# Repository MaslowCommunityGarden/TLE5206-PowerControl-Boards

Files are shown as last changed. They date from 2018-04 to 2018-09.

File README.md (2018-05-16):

# TLE5206 PowerControl Boards

PowerControl board based on the TLE5206. Thru-hole and SMD versions

# About the boards:

The standard Maslow PowerControl board uses a pair of simple surface-mount motor-control chips, the L298P013TR, to control the motors. Each chip can control two motors, up to total 4A divided between the motors. Only three motors are provisioned in the release version of the board. There has been concern about the current capacity of these chips and there have been instances where the chips have been damaged when software malfunctioned. Once a chip is damaged, the board would require replacing a 20-pin surface-mount chip to repair.

The TLE5206 offers higher current capacity, over-temperature and over-current detection and protection, along with a simpler package. In addition, there is a thru-hole version of the chip available that would allow a thru-hole version of the board, easier for some users to construct or repair. While the control pins are different from the L298 chips, the firmware requires very little change to work with the TLE5206.

This is a first stab at using the TLE5206 chips on the PowerControl board.
 -  The Electronics folder has EagleCAD board and schematic files for a SMD version and a thru-hole version. I've built and tested both.
 -  The Firmware has been merged with the main MaslowCNC Firmware branch. It adds three true PWM pins to the AUX group which might be used for spindle control with some software development. It doesn't implement the software over-current detection that the TLE5206 offers. For now, the chips sense the over-current or over-temperature condition and protect themselves by turning off the outputs. Use the Arduino IDE to upload the master firmware to control the TLE5206 board.

This design brings:
- separate controller chip for each motor
- higher current capacity (5A) per motor
- thru-hole version to aid hand assembly and repair
- board-mounted heat sinks for the thru-hole version
- mounting holes to match three of the Arduino mounting holes
- AUX pins moved to extended end of board
- 4 digital AUX pins
- 2 analog/digital AUX pins
- 3 PWM-capable digital AUX pins
- board version ID pins avoids using SPI pins

It doesn't bring:
- additional motor control channels
- software over-current or over-temperature sensing

# PCBs
======================

Layout

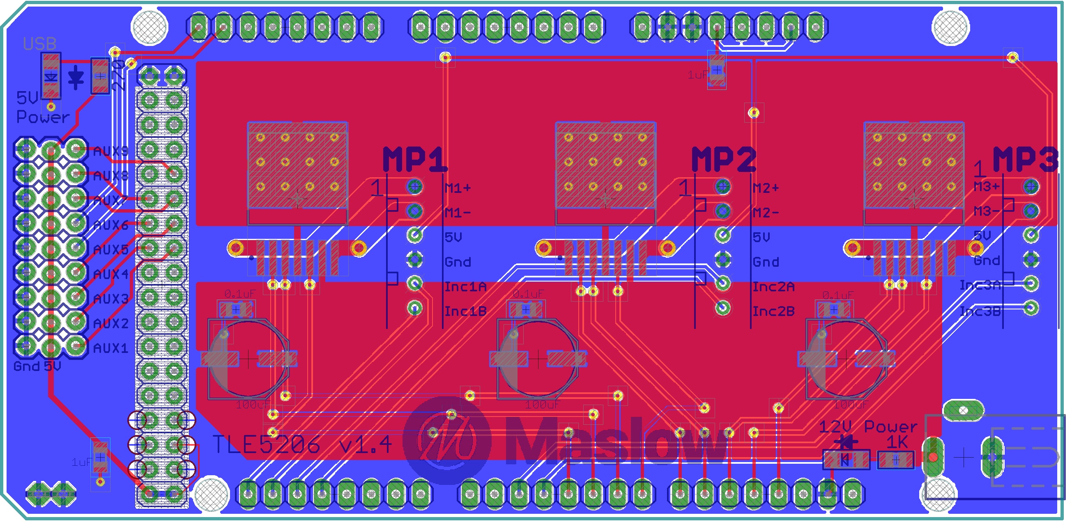
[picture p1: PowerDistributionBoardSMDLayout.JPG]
SMD Layout


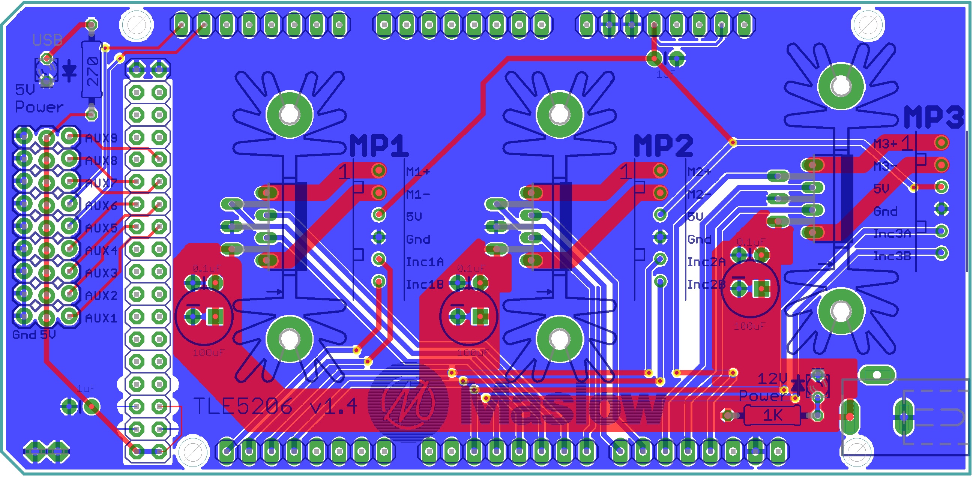
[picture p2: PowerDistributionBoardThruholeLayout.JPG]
Thruhole Layout


Schematic - SMD version

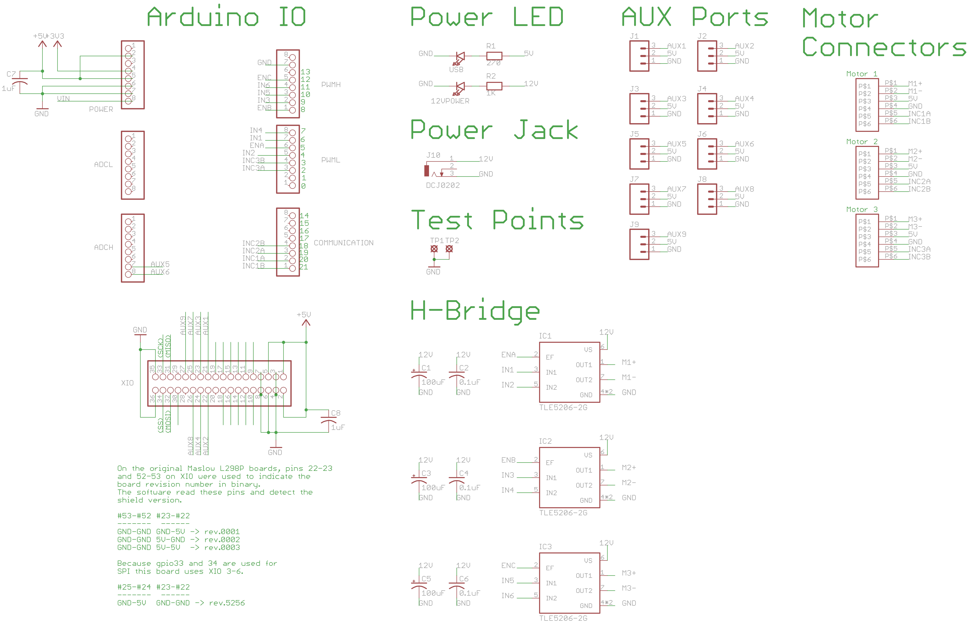
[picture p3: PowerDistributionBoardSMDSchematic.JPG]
SMD schematic


Schematic - Thruhole version

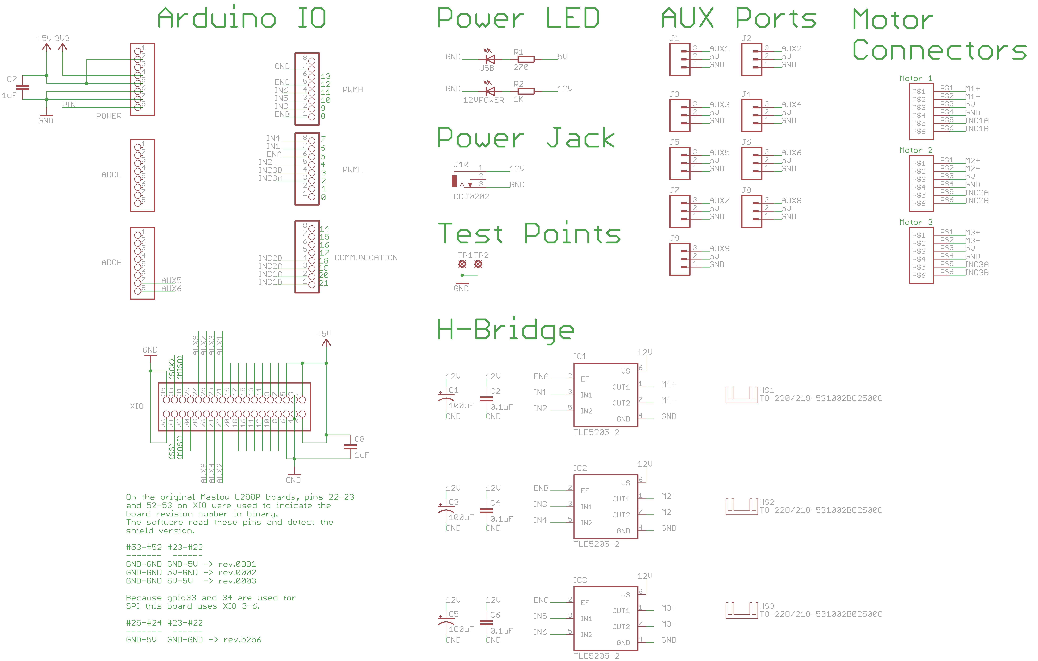
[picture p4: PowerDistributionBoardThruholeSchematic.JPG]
Thruhole Schematic


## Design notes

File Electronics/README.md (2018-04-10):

Maslow PCBs
======================

The TLE5206 offers over-temperature and over-current detection and protection.

This design brings:
- separate controller chip for each motor
- higher current capacity (5A) per motor
- thru-hole parts to aid hand assembly and repair
- board-mounted heat sinks for the thru-hole version
- mounting holes to match the Arduino Mega2560
- AUX pins on extended end of board
- 4 digital AUX pins
- 2 analog/digital AUX pins
- 3 PWM-capable AUX pins
- board version ID pins avoids using SPI pins

Layout
  - thru-hole
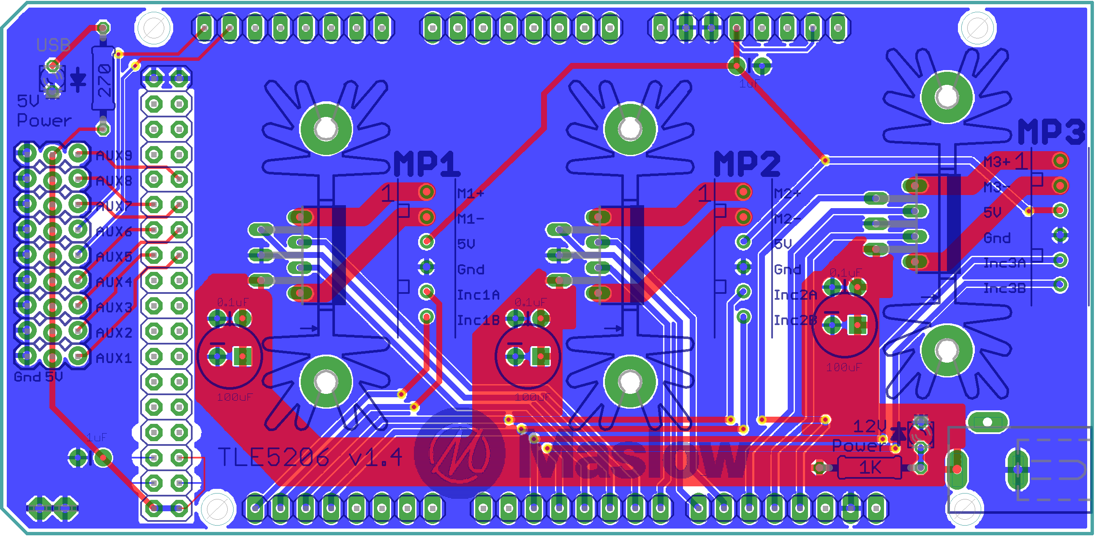
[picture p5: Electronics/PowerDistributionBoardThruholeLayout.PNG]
Layout

  - SMD
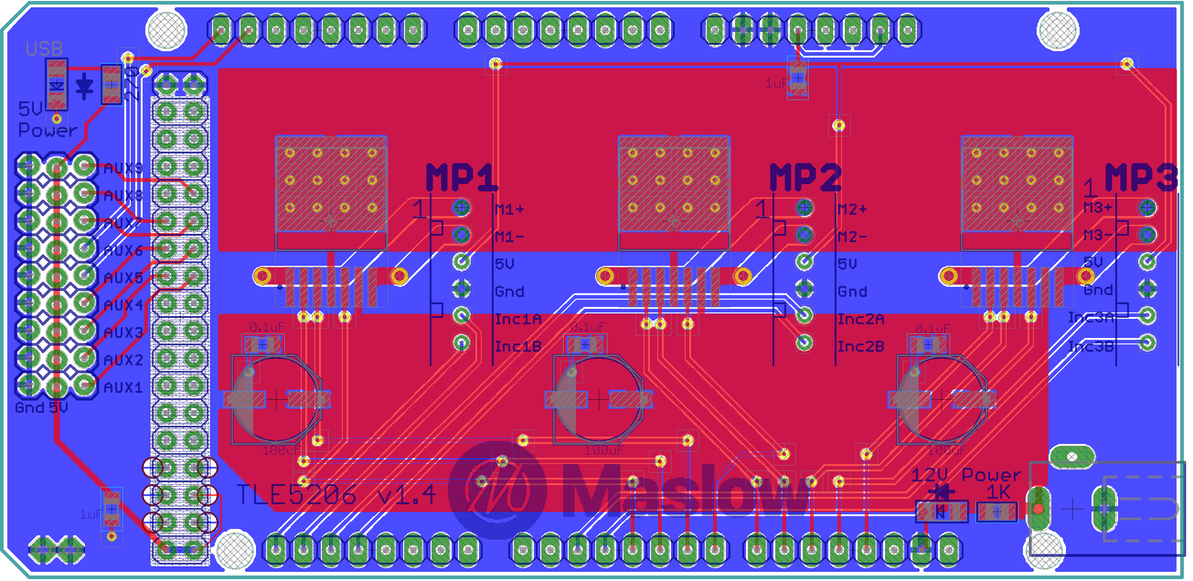
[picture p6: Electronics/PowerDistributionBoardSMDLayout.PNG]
Layout


Schematic
- thru-hole
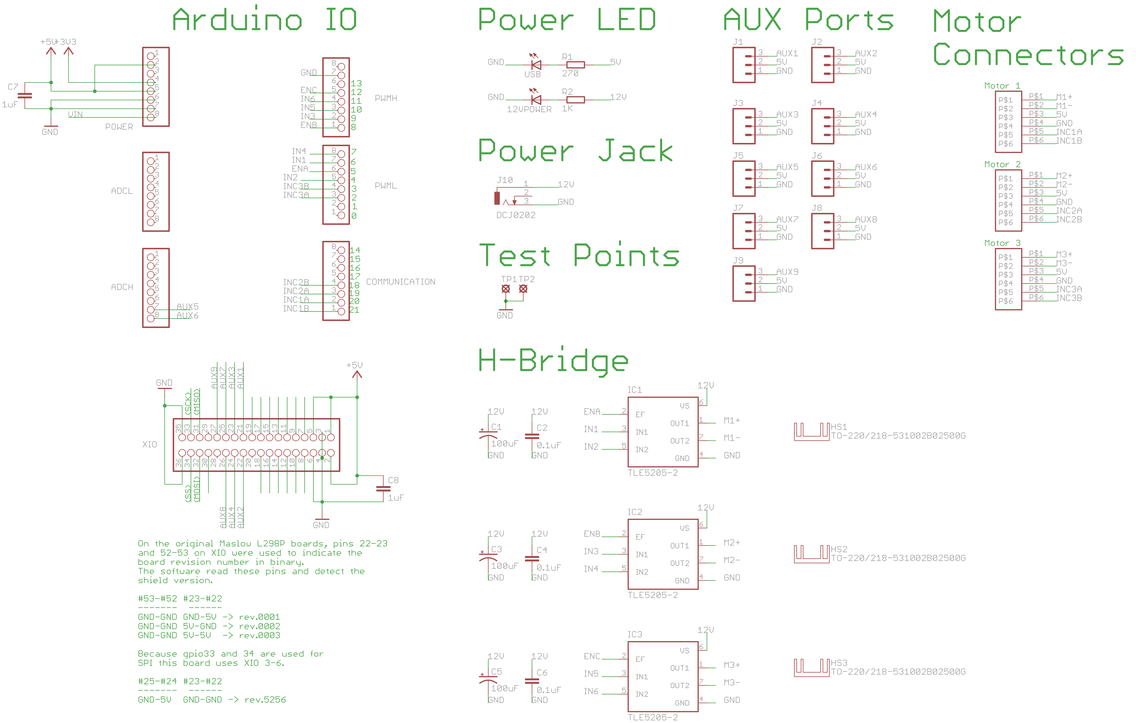
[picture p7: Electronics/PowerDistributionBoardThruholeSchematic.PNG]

- SMD
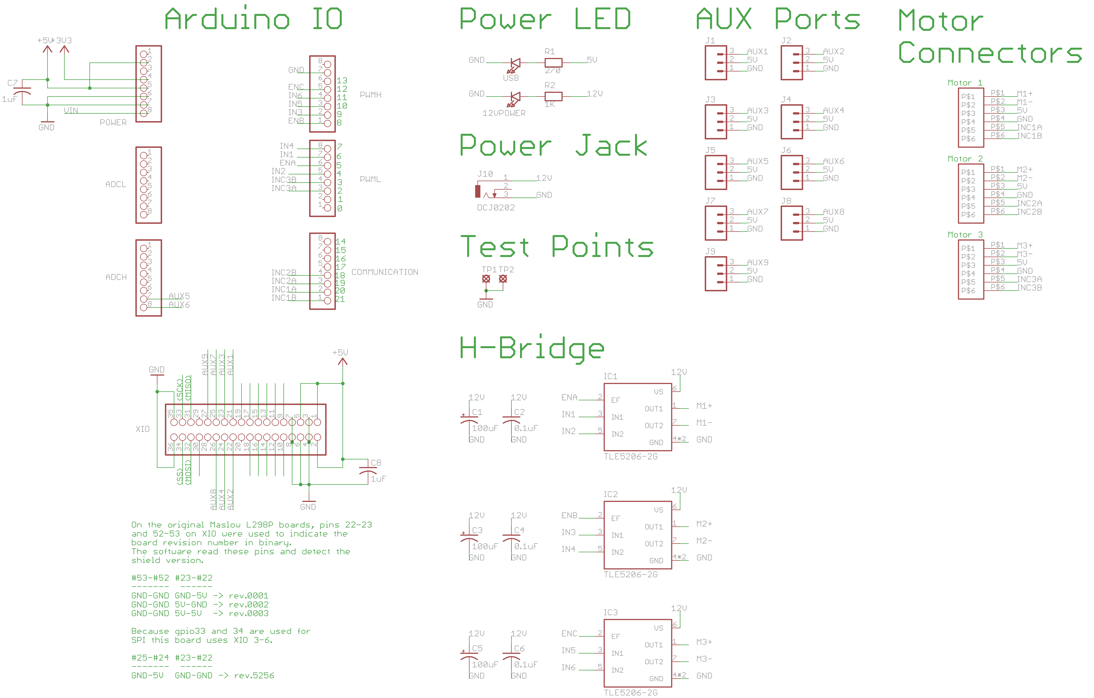
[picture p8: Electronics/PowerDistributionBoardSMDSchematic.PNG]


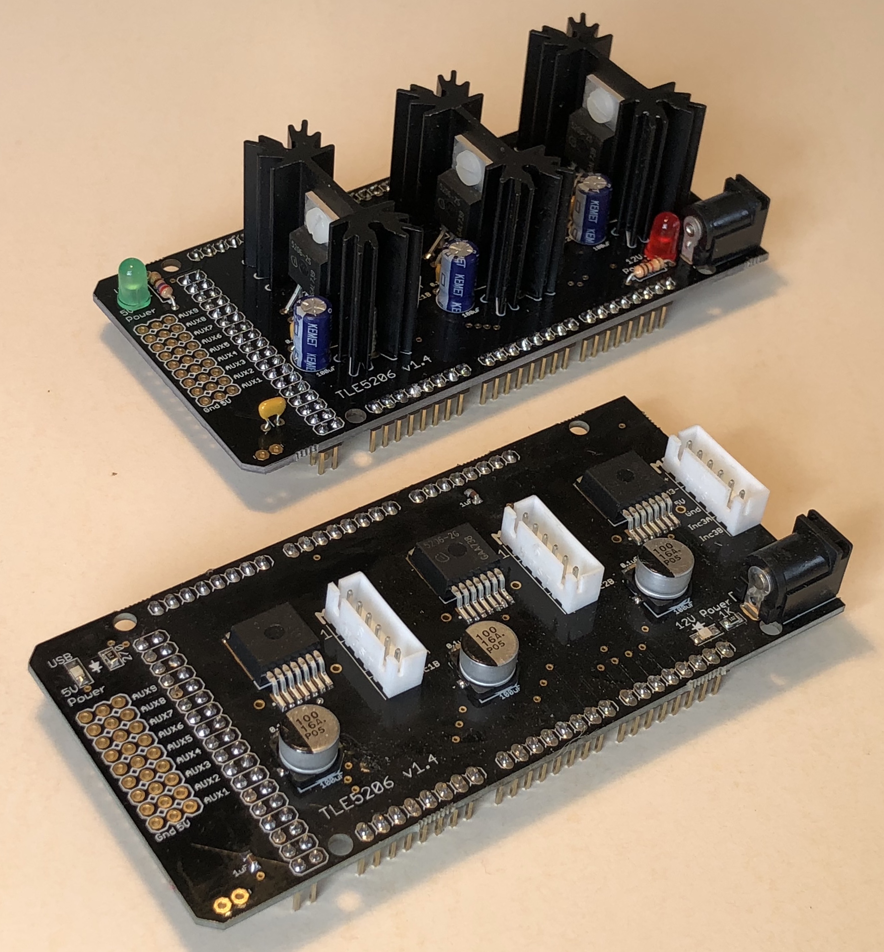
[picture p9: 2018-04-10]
mainpicture.jpg

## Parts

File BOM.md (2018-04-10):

The Electronics folder has BOM files for both versions of the board. Many web-based PCB houses accept an EagleCAD .brd file for ordering.
The Firmware has the branch of Firmware to use the boards.

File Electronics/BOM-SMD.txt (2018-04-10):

PCB BOM SMD

XH-Series Connectors: 455-2271-ND             3        MP1-3
Power Jack:           CP-202BH-ND             1        J10
1x8 .1" headers:      732-5321-ND             6        Arduino Pwr, ADCL, ADCH, Comm., PWML, PWMH
18x2 .1" headers:     732-5309-ND             1        XIO
H-Bridge:             TLE52062GAUMA1CT-ND     3        IC-1,2,3
Indicator LED Green:  475-1410-1-ND           2        LED 1: 5V, LED 2: 12V
Current Limiting R1:  RMCF0805JT270RCT-ND     1        R1
Current Limiting R2:  541-4162-1-ND           1        R2
25.4x34.93mm heatsink Mouser-532-374124B35G   3        N/A
Capacitors 100uF      PCE3879DKR-ND           3        C1, C3, C5
Capacitors 1uF        445-5146-1-N            2        C7,8
Capacitors 0.1uF      311-1361-1-ND           3        C2, C4, C6

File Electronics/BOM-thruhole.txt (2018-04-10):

PCB BOM-trhuhole

XH-Series Connectors: 455-2271-ND             3        MP1-3
Power Jack:           CP-202BH-ND             1        J10
1x8 .1" headers:      732-5321-ND             6        Arduino Pwr, ADCL, ADCH, Comm., PWML, PWMH
18x2 .1" headers:     732-5309-ND             1        XIO
H-Bridge:             TLE52062SAKSA1-ND       3        IC-1,2,3
Indicator LED Green:  160-1130-ND             1        LED 1: 5V
Indicator LED Red:    160-1127-ND             1        LED 2: 12V
Current Limiting R1:  1263-CF14JB270R-CHP     1        R1
Current Limiting R2:  1.0KQBK-ND              1        R2
25.4x34.93mm heatsink HS351-ND                3        N/A
Capacitors 100uF      399-6650-1-ND           3        C1, C3, C5
Capacitors 1uF        BC1168CT-ND             2        C7,8
Capacitors 0.1uF      BC1101CT-ND             3        C2, C4, C6
#4-40 x 1/4" Panhead Nylon machine screws     3
#4-40 nylon nuts                              3

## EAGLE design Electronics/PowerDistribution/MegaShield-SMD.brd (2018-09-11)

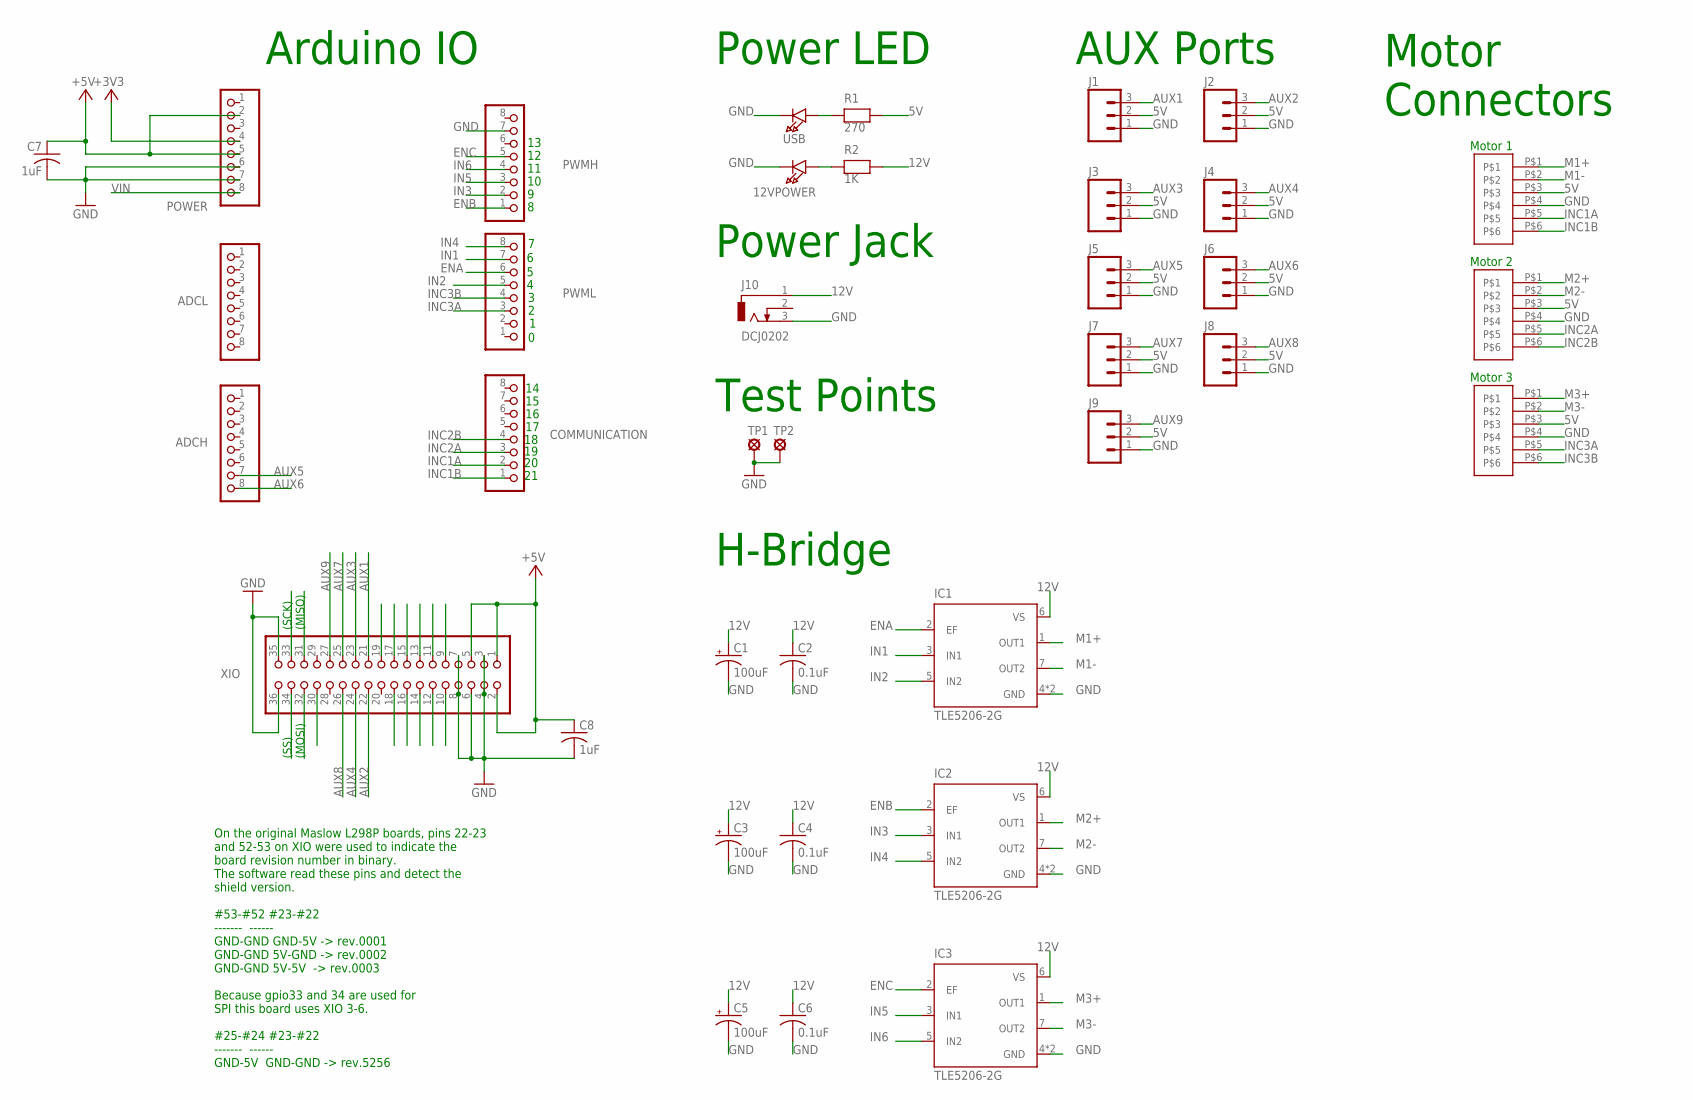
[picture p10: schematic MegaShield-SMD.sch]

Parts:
12VPOWER: LED1206; CHIPLED_1206
ADCH: 8x1F-H8.5; 1X08
ADCL: PINHD-1X8; 1X08
C1, C3, C5: 100uF; PANASONIC_E
C2, C4, C6: 0.1uF; C0805K
C7, C8: 1uF; C0805K
COMMUNICATION: PINHD-1X8; 1X08
IC1, IC2: TLE5206-2G; INF-PG-TO263-7-1_L_1PRIMARY
IC3: TLE5206-2G; INF-PG-TO263-7-1_L_1PRIMARY; DIGIKEY TLE5206-2S-ND
J1, J2, J3, J4, J5, J6, J7, J8, J9: M03LOCK; 1X03_LOCK
J10: DCJ0202
MP1, MP2, MP3: JST-PH-6; JST-PHR-6-SMD
POWER: 8x1F-H8.5; 1X08
PWMH: PINHD-1X8; 1X08
PWML: PINHD-1X8; 1X08
R1: 270; 0805
R2: 1K; 0805
TP1, TP2: LSP10
USB: LED1206; CHIPLED_1206
XIO: 18x2F-H8.5; 2X18

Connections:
5V: C7.1, C8.1, J1.2, J2.2, J3.2, J4.2, J5.2, J6.2, J7.2, J8.2, J9.2, MP1.P$3, MP2.P$3, MP3.P$3, POWER.2, POWER.5, R1.2, XIO.1, XIO.2, XIO.5
12V: C1.+, C2.1, C3.+, C4.1, C5.+, C6.1, IC1.6 (VS), IC2.6 (VS), IC3.6 (VS), J10.1, R2.2
+3V3: POWER.4
AUX1: J1.3, XIO.21
AUX2: J2.3, XIO.22
AUX3: J3.3, XIO.23
AUX4: J4.3, XIO.24
AUX5: ADCH.7, J5.3
AUX6: ADCH.8, J6.3
AUX7: J7.3, XIO.25
AUX8: J8.3, XIO.26
AUX9: J9.3, XIO.27
ENA: IC1.2 (EF), PWML.6
ENB: IC2.2 (EF), PWMH.1
ENC: IC3.2 (EF), PWMH.5
GND: 12VPOWER.C, C1.-, C2.2, C3.-, C4.2, C5.-, C6.2, C7.2, C8.2, IC1.4 (GND), IC1.8 (GND), IC2.4 (GND), IC2.8 (GND), IC3.4 (GND), IC3.8 (GND), J1.1, J2.1, J3.1, J4.1, J5.1, J6.1, J7.1, J8.1, J9.1, J10.3, MP1.P$4, MP2.P$4, MP3.P$4, POWER.6, POWER.7, PWMH.7, TP1.MP, TP2.MP, USB.C, XIO.3, XIO.4, XIO.6, XIO.7, XIO.8, XIO.35, XIO.36
IN1: IC1.3 (IN1), PWML.7
IN2: IC1.5 (IN2), PWML.5
IN3: IC2.3 (IN1), PWMH.2
IN4: IC2.5 (IN2), PWML.8
IN5: IC3.3 (IN1), PWMH.3
IN6: IC3.5 (IN2), PWMH.4
INC1A: COMMUNICATION.2, MP1.P$5
INC1B: COMMUNICATION.1, MP1.P$6
INC2A: COMMUNICATION.3, MP2.P$5
INC2B: COMMUNICATION.4, MP2.P$6
INC3A: MP3.P$5, PWML.3
INC3B: MP3.P$6, PWML.4
M1+: IC1.1 (OUT1), MP1.P$1
M1-: IC1.7 (OUT2), MP1.P$2
M2+: IC2.1 (OUT1), MP2.P$1
M2-: IC2.7 (OUT2), MP2.P$2
M3+: IC3.1 (OUT1), MP3.P$1
M3-: IC3.7 (OUT2), MP3.P$2
unnamed: R1.1, USB.A
unnamed: 12VPOWER.A, R2.1
PA6: XIO.9
PA7: XIO.10
PB0: XIO.34
PB1: XIO.33
PB2: XIO.32
PB3: XIO.31
PC0: XIO.18
PC1: XIO.17
PC2: XIO.16
PC3: XIO.15
PC4: XIO.14
PC5: XIO.13
PC6: XIO.12
PC7: XIO.11
PD7: XIO.19
PL0: XIO.30
VIN: POWER.8

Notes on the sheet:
Motor 1
Motor 2
H-Bridge
Power LED
Power Jack
Arduino IO
AUX Ports
Motor Connectors
Motor 3
On the original Maslow L298P boards, pins 22-23 and 52-53 on XIO were used to indicate the board revision number in binary. The software read these pins and detect the shield version. #53-#52 #23-#22 ------- ------ GND-GND GND-5V -> rev.0001 GND-GND 5V-GND -> rev.0002 GND-GND 5V-5V -> rev.0003 Beca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
(SS)
(MOSI)
(SCK)
(MISO)
Test Points

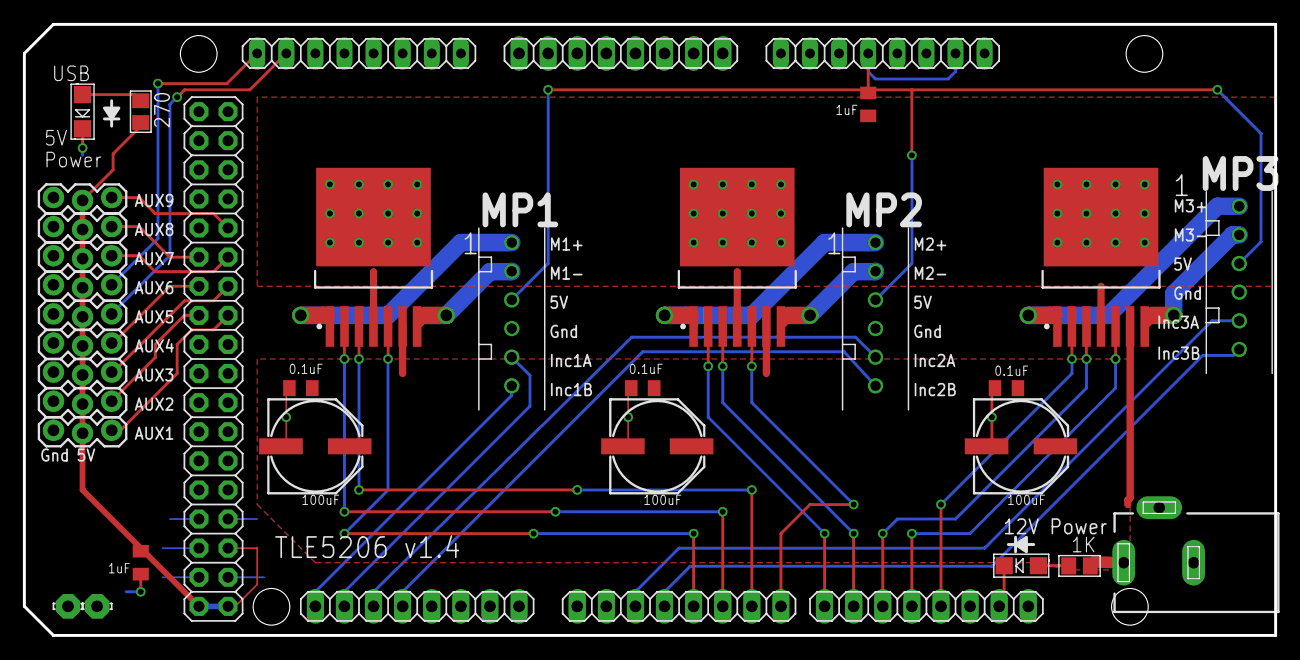
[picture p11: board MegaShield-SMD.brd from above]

Board: 2 copper layers, 109.2 x 53.3 mm, 37 parts (0 on the bottom side), 35 nets.

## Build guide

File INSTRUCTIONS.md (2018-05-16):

The circuit boards are electronically the same, one uses thru-hole parts for easier assembly. The thru-hole board uses heat sinks that can be soldered to the board for rigidity.

Many web-based PCB houses will accept an EagleCAD .brd file for manufacturing.

The firmware has been merged with the main MaslowCNC Firmware branch. Use the Arduino IDE to upload the master firmware to control the TLE5206 board.

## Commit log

2018-04-10 Add the contents
    [MegaShield-SMD.brd, MegaShield-SMD.sch, MegaShield-thruhole.brd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]
2018-04-10 Add schematics and layouts to Readme
2018-04-10 Correct schematic links
2018-06-05 Convert ROBOT.md file to use json format
    Using the json format will make it easier for us to store meta data to categorize and tag projects. The garden is filling up (which is AMAZING!!) but its starting to get a little cluttered. I am hopi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
2018-09-09 Move MP3 to prevent Inc3B from shorting against USB connector of Arduino Mega
    [MegaShield-SMD.brd]

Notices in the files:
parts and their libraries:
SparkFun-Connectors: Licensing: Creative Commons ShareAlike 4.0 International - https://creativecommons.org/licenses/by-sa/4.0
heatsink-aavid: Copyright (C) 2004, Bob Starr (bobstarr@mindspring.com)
